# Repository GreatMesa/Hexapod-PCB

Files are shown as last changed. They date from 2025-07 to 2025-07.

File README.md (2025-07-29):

# Hexapod-PCB
### 4-Layer PCB for the Arduino Hexapod

## Introduction
This PCB is a 4-Layer hexapod for servo applications. It containes a signal layer for all the servo pwm pins and a uniform ground + power plane for the servos spesifically. The reason while I decided to go through this project is because I wanted a way that I can adjust the voltage level of the servos as depending on the voltage of the servos the speed and tourque is affected. This also will organize my wire managment by a lot since I don't have to extrapolate my electonics to a bunch of breadboards.

## Goals
Here are the main goals of this PCB:
- Make a PCB that can manage 18 seperate servos simutaneously.
- Have uniform and stable power for all 18 servos.
- Make calculations using a inertial sensor for inverse kinematics.
- Use NRF protocol to communicate with a RC transmitter.
- Have indication for the hexapod status using LEDs and a Buzzer.
## PCB 3D Model



## PCB Picture



## Bill of Materials
| Item Name | Price (USD) | Quantity | Total Price (USD) | Purchase Link |
|---|---|---|---|---|
| PCB Order | $33.15 | 1 | $33.15 | [Link](https://www.pcbway.com/QuickOrderOnline.aspx) |
| Teensy 4.1 | $37.50 | 1 | $37.50 | [Link](https://www.amazon.com/PJRC-Cortex-M7-Processor-iMXRT1062-Without/dp/B088JY7P2H) |
| Male Pin Header Strips  | OWNED | OWNED | OWNED | [Link](https://www.amazon.com/Straight-Breakaway-Connector-Breadboard-Electronic/dp/B09MYBRW3F) |
| Female Pin Header Strips| $0.99 | 1 | $0.99 | [Link](https://www.aliexpress.us/item/2251832850099221.html) |
| 7.4 5200mAh Lipo | $15.97 | 1 | $15.97 | [Link](https://www.amazon.com/Zeee-5200mAh-Battery-Truggy-Airplane/dp/B06ZYRCPS3) |
| ACS712 Current Sensor | $1.15 | 1 | $1.15 | [Link](https://lcsc.com/product-detail/Current-Sensors_ALLEGRO-ACS712ELCTR-05B-T_C44471.html) |
| WS2812B Individual LEDs | $0.41 | 1 | $0.41 | [Link](https://lcsc.com/product-detail/RGB-LEDs-Built-in-IC_XINGLIGHT-XL-5050RGBC-WS2812B_C2843785.html) |
| SN74HCT125D | $1.06 | 1 | $1.06 | [Link](https://lcsc.com/product-detail/Buffers-Drivers-Receivers-Transceivers_TI-SN74HCT125DR_C352957.html) |
| 10pc Buzzers | $0.49 | 1 | $0.49 | [Link](https://lcsc.com/product-detail/Buzzers_YUEXIN-YX-YD2319_C781874.html) |
| OLED | $1.97 | 1 | $1.97 | [Link](https://lcsc.com/product-detail/OLED-Display_HS-HS96L03W2C03_C5248080.html) |
| **Total Cost** | | | **$90.72** | |

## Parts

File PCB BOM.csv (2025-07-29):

Item Name | Price (USD) | Quantity | Total Price (USD) | Purchase Link
PCB Order | $33.15 | 1 | $33.15 | https://www.pcbway.com/QuickOrderOnline.aspx
Teensy 4.1 | $37.50 | 1 | $37.50 | https://www.amazon.com/PJRC-Cortex-M7-Processor-iMXRT1062-Without/dp/B088JY7P2H
Male Pin Header Strips | OWNED | OWNED | OWNED | https://www.amazon.com/Straight-Breakaway-Connector-Breadboard-Electronic/dp/B09MYBRW3F
Female Pin Header Strips | $0.99 | 1 | $0.99 | https://www.aliexpress.us/item/2251832850099221.html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
7.4 5200aH Lipo | $15.97 | 1 | $15.97 | https://www.amazon.com/Zeee-5200mAh-Battery-Truggy-Airplane/dp/B06ZYRCPS3
ACS712 Current Sensor | $1.15 | 1 | $1.15 | https://lcsc.com/product-detail/Current-Sensors_ALLEGRO-ACS712ELCTR-05B-T_C44471.html?s_z=n_ACS712%2520
WS2812B Individual LEDS | $0.41 | 1 | $0.41 | https://lcsc.com/product-detail/RGB-LEDs-Built-in-IC_XINGLIGHT-XL-5050RGBC-WS2812B_C2843785.html?s_z=n_ws2812b
SN74HCT125D | $1.06 | 1 | $1.06 | https://lcsc.com/product-detail/Buffers-Drivers-Receivers-Transceivers_TI-SN74HCT125DR_C352957.html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
10pc Buzzers | $0.49 | 1 | $0.49 | https://lcsc.com/product-detail/Buzzers_YUEXIN-YX-YD2319_C781874.html?s_z=n_buzzer
OLED | $1.97 | 1 | $1.97 | https://lcsc.com/product-detail/OLED-Display_HS-HS96L03W2C03_C5248080.html?s_z=n_oled%25200.96
Total Cost |  |  | $90.72

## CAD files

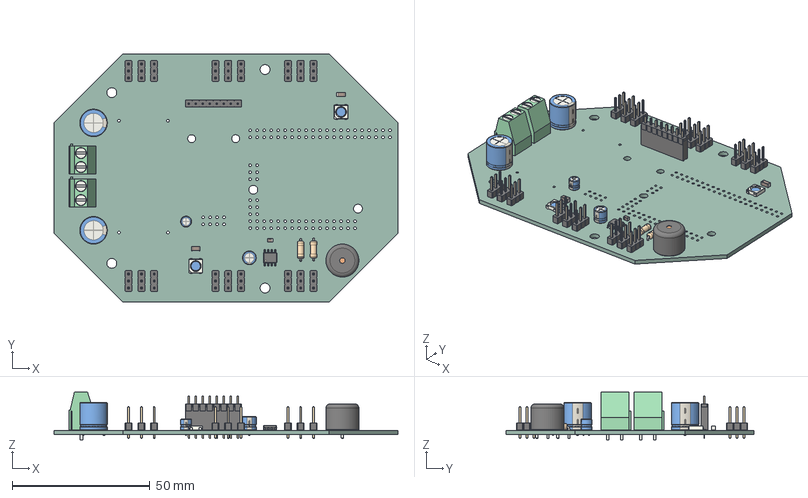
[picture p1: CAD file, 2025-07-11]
Hexapod V2/Hexapod V2.step
125.0 x 90.0 x 17.3 mm
PinHeader_1x03_P254mm_Vertical x 18
LED_WS2812B_PLCC4_50x50mm_P32mm x 2
C_1206_3216Metric x 2
TerminalBlock_Phoenix_MKDS_15_2_508_1x02_P508mm_Horizontal x 2
CP_Radial_D40mm_P200mm
CP_Radial_D100mm_P750mm x 2
SOIC_8_39x49mm_P127mm
Buzzer_12x95RM76
CP_Radial_D50mm_P200mm
C_0805_2012Metric
R_Axial_DIN0207_L63mm_D25mm_P762mm_Horizontal x 2
PinHeader_1x08_P254mm_Vertical
PinSocket_1x08_P2.54mm_Vertical
_autosave-Hexapod V2_PCB

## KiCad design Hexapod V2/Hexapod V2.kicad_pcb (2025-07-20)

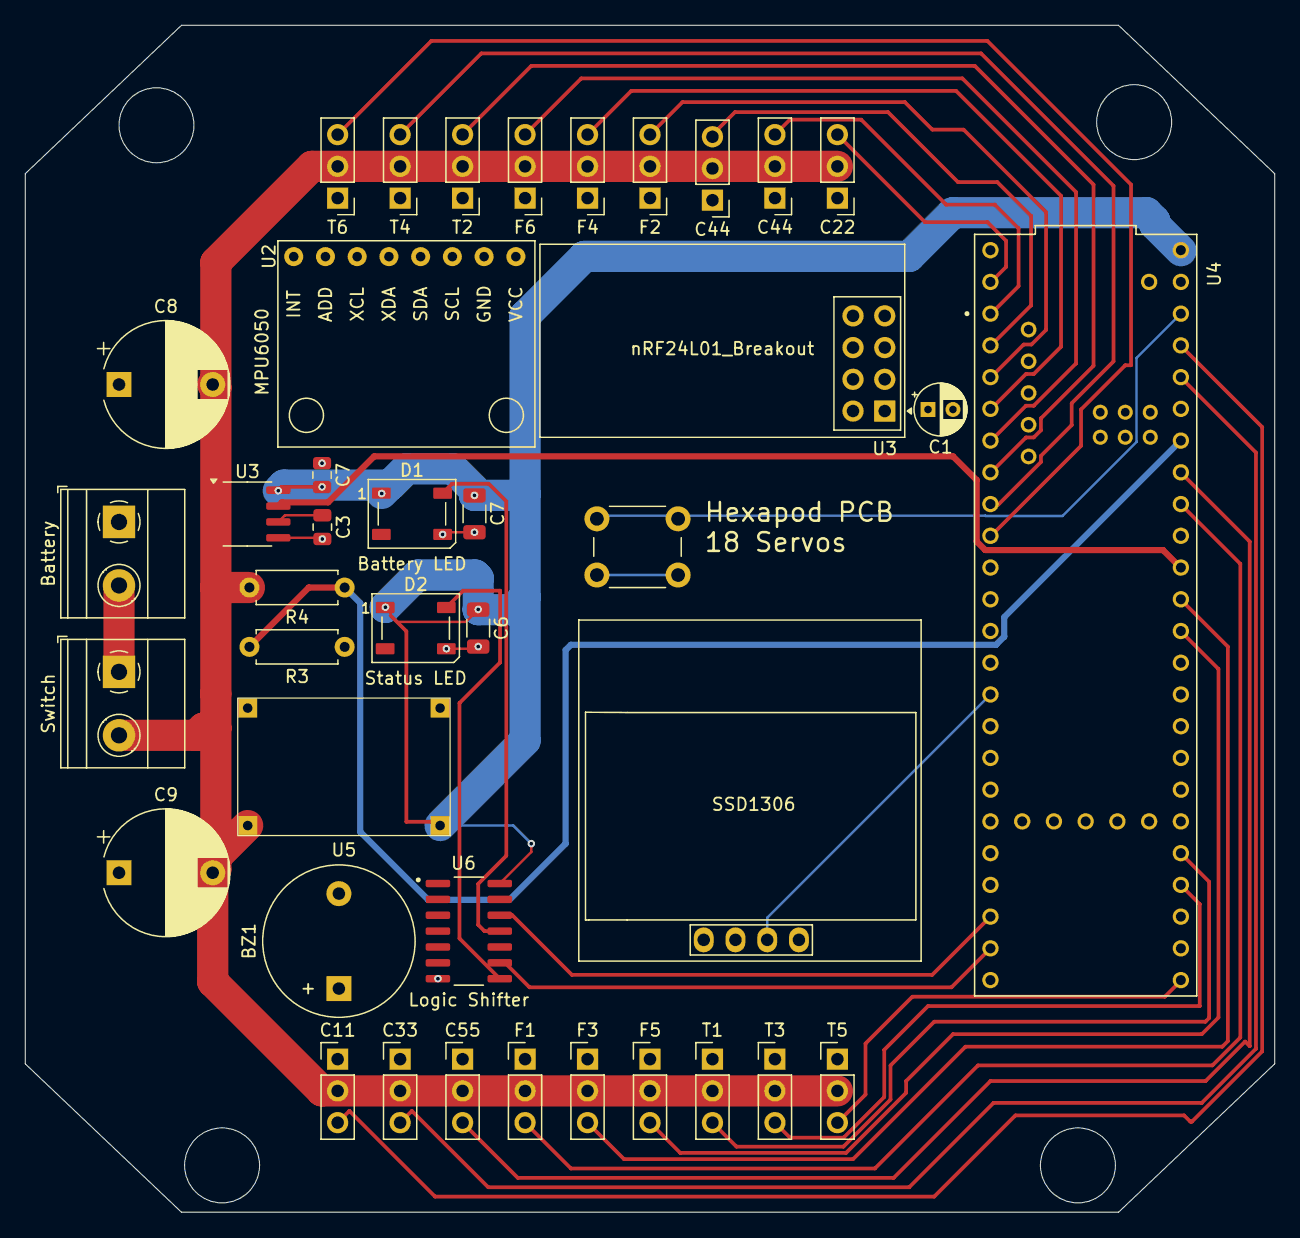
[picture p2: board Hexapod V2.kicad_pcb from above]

Board: 4 copper layers, 100.0 x 95.0 mm, 39 parts (0 on the bottom side), 36 nets.

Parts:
BZ1: Buzzer; Buzzer_12x9.5RM7.6
C1: 16V 22μF; CP_Radial_D4.0mm_P2.00mm
C3, C7: 102 1nf; C_0805_2012Metric
C6, C7#2: 104 0.1μF; C_1206_3216Metric
C8, C9: 16V 1mF; CP_Radial_D10.0mm_P7.50mm
C11, C22, C33, C44, C44#2, C55: Conn_01x03_Pin; PinHeader_1x03_P2.54mm_Vertical
D1: Battery LED; LED_WS2812B_PLCC4_5.0x5.0mm_P3.2mm
D2: Status LED; LED_WS2812B_PLCC4_5.0x5.0mm_P3.2mm
F1, F2, F3, F4, F5, F6: Conn_01x03_Pin; PinHeader_1x03_P2.54mm_Vertical
J2: Battery; TerminalBlock_Phoenix_MKDS-1,5-2-5.08_1x02_P5.08mm_Horizont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
J3: Switch; TerminalBlock_Phoenix_MKDS-1,5-2-5.08_1x02_P5.08mm_Horizont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
R3, R4: 100kΩ; R_Axial_DIN0207_L6.3mm_D2.5mm_P7.62mm_Horizontal
SSD1306: 128x64OLED
T1, T2, T3, T4, T5, T6: Conn_01x03_Pin; PinHeader_1x03_P2.54mm_Vertical
U2: MPU6050; module_mpu6050
U3: ACS712xLCTR-05B; SOIC-8_3.9x4.9mm_P1.27mm
U3#2: nRF24L01_Breakout
U4: Teensy 4.1; MODULE_DEV-16771
U5: Buck
U6: Logic Shifter; SOIC127P600X175-14N

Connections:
+3.3V: C1.1, SSD1306.2, U2.1 (VCC), U3#2.2, U4.3.3V_1 (3.3V), U4.3.3V_2 (3.3V), U4.3.3V_3 (3.3V)
+5V: C6.1, C7.2, C7#2.1, D1.1 (VDD), D2.1 (VDD), U3.8 (VCC), U4.5V, U4.VIN, U5.2, U6.14
Buzzer: BZ1.1 (+), U4.27 (A13)
CE: U3#2.3, U4.26 (A12)
CSN: U3#2.4, U4.10 (CS1)
Current Reading: U3.7 (VIOUT), U4.16 (A2)
GND: BZ1.2 (-), C1.2, C3.2, C6.2, C7.1, C7#2.2, C8.1, C9.1, C11.1, C22.1, C33.1, C44.1, C44#2.1, C55.1, D1.3 (VSS), D2.3 (VSS), F1.1, F2.1, F3.1, F4.1, F5.1, F6.1, J2.1, R3.1, SSD1306.1, T1.1, T2.1, T3.1, T4.1, T5.1, T6.1, U2.2 (GND), U3.5 (GND), U3#2.1, U4.GND1 (GND), U4.GND2 (GND), U4.GND3 (GND), U4.GND4 (GND), U4.GND5 (GND), U5.1, U5.3, U6.7
LED1: D1.4 (DIN), U4.30 (CRX3), U6.11, U6.12
LED2: D2.4 (DIN), U4.31 (CTX3), U6.8, U6.9
MISO: U3#2.7, U4.12 (MISO)
MOSI: U3#2.6, U4.11 (MOSI)
unnamed: C3.1, U3.6 (FILTER)
unnamed: U4.USB_GND1 (USB_GND), U4.USB_GND2 (USB_GND)
S1: C22.3, U4.0 (RX1)
S2: C44.3, U4.1 (TX1)
S3: C44#2.3, U4.2 (OUT2)
S4: F2.3, U4.3 (LRCLK2)
S5: F4.3, U4.4 (BCLK2)
S6: F6.3, U4.5 (IN2)
S7: T2.3, U4.6 (OUT1D)
S8: T4.3, U4.7 (RX2)
S9: T6.3, U4.8 (TX2)
S10: T5.3, U4.33 (MCLK2)
S11: T3.3, U4.36 (CS2)
S12: T1.3, U4.37 (CS3)
S13: F5.3, U4.14 (A0)
S14: F3.3, U4.15 (A1)
S15: F1.3, U4.18 (A4)
S16: C55.3, U4.19 (A5)
S17: C33.3, U4.22 (A8)
S18: C11.3, U4.23 (A9)
SCK: U3#2.5, U4.13 (SCK)
SCL: U2.3 (SCL), U4.24 (A10)
SDA: U2.4 (SDA), U4.25 (A11)
VD Reading: R3.2, R4.1, U4.20 (A6)
VIN: C8.2, C9.2, C11.2, C22.2, C33.2, C44.2, C44#2.2, C55.2, F1.2, F2.2, F3.2, F4.2, F5.2, F6.2, J2.2, J3.1, J3.2, R4.2, T1.2, T2.2, T3.2, T4.2, T5.2, T6.2, U3.1 (IP+), U3.2 (IP+), U3.3 (IP-), U3.4 (IP-), U5.4

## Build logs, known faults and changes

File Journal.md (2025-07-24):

---
title: "Hexapod PCB"
author: "Chinedu Okpala"
description: "4-Layer PCB for Robotic hexapod"
created_at: "2025-6-26"
---
# 4-Layer Hexapod PCB.

##Total Hours: 36

## Reaserch 6/26/2025 3 Hours

In order to create a 4-layer PCB, I knew that I needed to first look into how I should go about it. The main reason why I wanted to use a 4-layer board was due to two factors:

- Uniform power distribution for all 18 servos.
- Space for all the traces on the pcb.

Uniform power planes allow for better power distribution while also protecting signal integrity to some degree. After looking into different configurations, I decided to layer my 4-layer PCB as this:

1. Signal
2. Ground
3. Power
4. Back

This formation allows me to protect the main signal integrity of the servos due to it being near the ground plane. Thats the main thing but the back also allows me to do leftover traces.

## Circuit Schematic 6/27/2025 - 6/28/2025 6 Hours

This circuit diagram took quite the time due to stuff from my past arduino shield needing to be revamped. The one thing that stayed constant was the pins schematic that I could just transfer over. This was the pins shcematic for the pcb:



The next part that I decided to tackle was the arduino mega pro that I would be using. All I needed to do was to look at an arduino mega pro 2560 as a refrence to see the best possible routing digital pins. This was fairly simple and after adding additional analog pins that I would be using later, this was the arduino mega pro schematic:



The next step was the NRF2401+. The datasheet recommended to use a capacitance of at least 10.1 nano farads. So I decided to simply use a 22 nf capacitor since I can use one from a cap kit that I had. Besides that it was pretty simple. This was my schematic:



The Inertial sensor (MPU6050) which I am using to deduce the accelerations of the robot is next. It was reccomended that the sda and scl connections had pull up resistors with 4.7k ohms. This was my schematic:



Looking at the indicators for my PCB (2 LEDS & 1 Buzzer) I just decided to use the first buzzer I found online due to its cheapness not affecting performances. For the LEDs I am using the WS2812B LEDs due to their multicolor features and ease of use. Besides this the LEDs also needed a ceramic cap for signal decoupling purposes. THese were the schematics for the buzzer and leds respectively:


(Buzzer)


(LEDs)

Finally, probably the most important part is the power supply. The main thing that I need from this power supply is a constant voltage so that in cases where a sservo moving can cause a voltage disturbance or some other wacky stuff I can still get a smooth voltage. I decided to use 2 bulky capacitors that combat changes in voltage. Also some other things that I added was a voltage divider to measure voltage and a current IC to measure current. This was the power supply shcematic that I have cooked up:



## PCB Routing / Editing 6/29/25 - 7/7/2025 15 Hours

Something to note into how this part took so so long is that it went through multiple variations. The first thing I needed to do was to position all the components in a way that I could route them. This was the arrangemnt that I came up with:



Nex was the actual routing part of this PCB. But as I was thinking about the circuit I realized something: the arduino & the servos needed a different power supply. Since my arduino mega pro takes a minimum of 7V while the maximum that the servos should be getting is 6.8V, which I possibly wanted to get lower for higher speed. I decided that I would need to attach a buck converter onto the actual board. However, I was not sure which voltage to use and which speed I wanted. After I finished routing everything, this was my final PCB:



## A Teensy Update 7/16/25 - 7/20/25 10 Hours
After getting my project rejected twice. I decided that I needed to change the size of the circuit board. I decided to replace the arduino mega pro with the Teensy 4.1 due to is lower size and it being a much better microcontroller. This was a simple fix as all I needed to do was look at the pwm ports on the teensy and see what I needed to swap. This was the teensy schematic I chalked up:



Funny thing, since the logic level was lower than the 3.5V (0.7VDD) needed, I needed to use a logic converter. I also added a OLED & 2 buttons so that I can interact with the sensors on board. Besides those fixes and the overall rerouting of the board, there was not any notable changes. This was the final schematic & 3D Model:

### PCB Layout



### PCB 3D Model



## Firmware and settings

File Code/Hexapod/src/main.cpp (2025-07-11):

#include <Arduino.h>

#include <Servo.h>

Servo myservo;  // create servo object to control a servo

int potpin = 0;  // analog pin used to connect the potentiometer
int val;    // variable to read the value from the analog pin

void setup() {
  myservo.attach(9);  // attaches the servo on pin 9 to the servo object
}

void loop() {
  val = analogRead(potpin);            // reads the value of the potentiometer (value between 0 and 1023)
  val = map(val, 0, 1023, 0, 180);     // scale it to use it with the servo (value between 0 and 180)
  myservo.write(90);                  // sets the servo position according to the scaled value
  delay(15);                           // waits for the servo to get there
}

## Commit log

2025-07-11 Submission commit
    [Hexapod V2.kicad_pcb, Hexapod V2.kicad_sch, Hexapod V2.step]
2025-07-12 Update and rename PCB BOM - Sheet1 (1).csv to PCB BOM.csv
    [PCB BOM - Sheet1 (1).csv, PCB BOM.csv]
2025-07-20 Added Teensy
    [Hexapod V2-B_Mask.gbr, Hexapod V2-B_Paste.gbr, Hexapod V2-B_Silkscreen.gbr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]
2025-07-20 Update PCB BOM.csv
    [PCB BOM.csv]
